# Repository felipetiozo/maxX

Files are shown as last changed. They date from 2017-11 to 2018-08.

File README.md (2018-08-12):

# maxX
Braço Robótico para fins educacionais
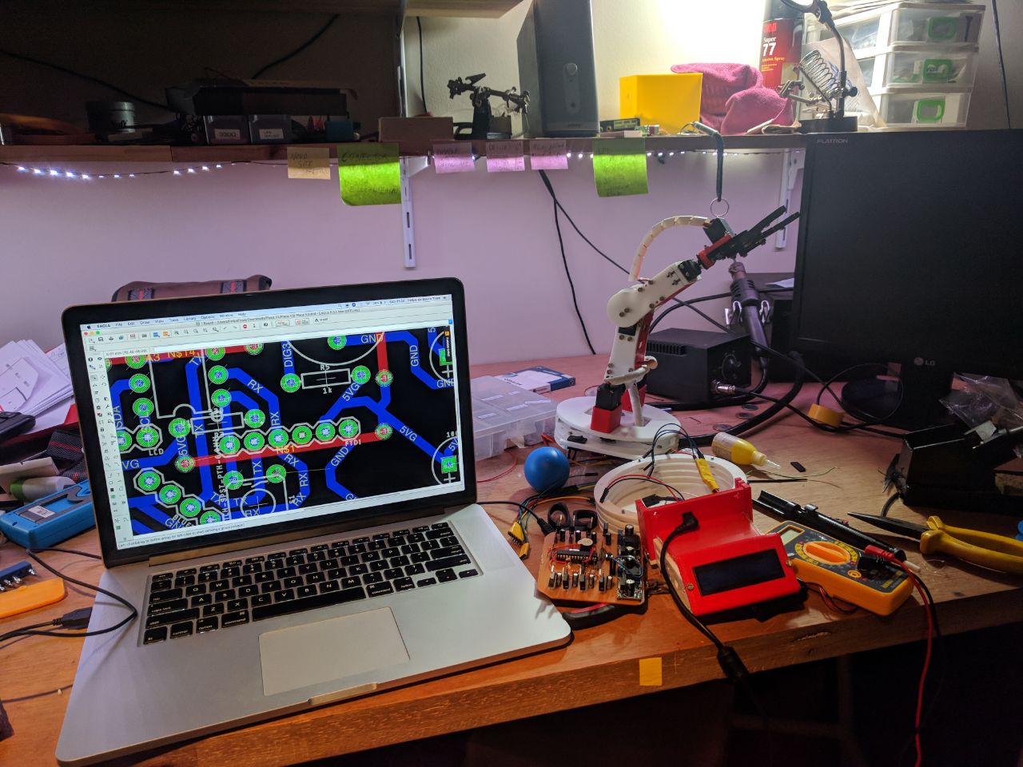
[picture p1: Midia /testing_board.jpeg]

<p align="center";> <b> Dia de testes do braço </b> </p>

# Divisões do projeto
* [`Software`](https://github.com/felipetiozo/maxX/tree/master/Software): Contem todas bibliotecas e código final do braço.
* [`Eletronica`](https://github.com/felipetiozo/maxX/tree/master/Eletronica): Possui todo esquema eletronico e o modelo final da PCB.
* [`Mecânica`](https://github.com/felipetiozo/maxX/tree/master/Mecanica): Todos arquivos .sldprt e .dxf do projeto.

## Eletronica
A PCB (Printed board circuit) do projeto foi construida no software [EAGLE(v8.3.1)](https://www.autodesk.com/products/eagle/overview) e fresada em uma mini cnc. [(Othermill)](https://www.bantamtools.com/)
### Lista de materiais 
| Qtd | Item | Loja | R$ |
|-----|---|-----|-----|
| 6 | MG995 Servo Motor | [Jsumo](http://www.jsumo.com/mg995-metal-gear-rc-servo-motor-towerpro) | 30,00 | 
| 1 | ATmega328P | [B.E](http://www.baudaeletronica.com.br/kit-arduino-atmega328p-bootloader.html) | 17,81 | 
| 2 | Encoder Decoder KY-040 | [Robocore](https://www.pololu.com/product/713) | 11,00 | 
| 1 | LCD 16x2 i2c | [Robocore](https://www.robocore.net/loja/produtos/lcd-16x2-5v-com-interface-i2c.html) | 49,00 | 
| 1 | FTDI Basic Breakout - 3.3V | [Sparkfun](https://www.sparkfun.com/products/9873) | 38,00 | 
| 2 | LM2596 | [B.E](http://www.baudaeletronica.com.br/modulo-regulador-de-tensao-lm2596.html) | 10,97 | 
| 1 | Fonte 12V 3A | [B.E](http://www.baudaeletronica.com.br/fonte-chaveada-12vdc-3a.html) | 48,37 | 

## Mecânica
O projeto mecânico foi desenvolvido no software de CAD [SolidWorks](http://www.solidworksbrasil.com.br/) e foi construido em 5 versões até chegar a final. Todas as peças foram impressas em 3D e cortadas em máquinas de corte a laser.

### Lista de materiais
| Qtd | Item | Loja | R$ |
|-----|---|-----|-----|
| 1 | Garra Robótica Croc | [Robocore](https://www.robocore.net/loja/produtos/garra-robotica-croc.html) | 29,00 | 
| 2 | Ball Caster with 3/8″ Metal Ball | [Pololu](https://www.pololu.com/product/951) | 6,50 | 

## Software
O software foi desenvolvido em cima da IDE [Arduino](https://www.arduino.cc/) e está dividido em diversas funções para uma utilização mais fácil.

# Contribuidores

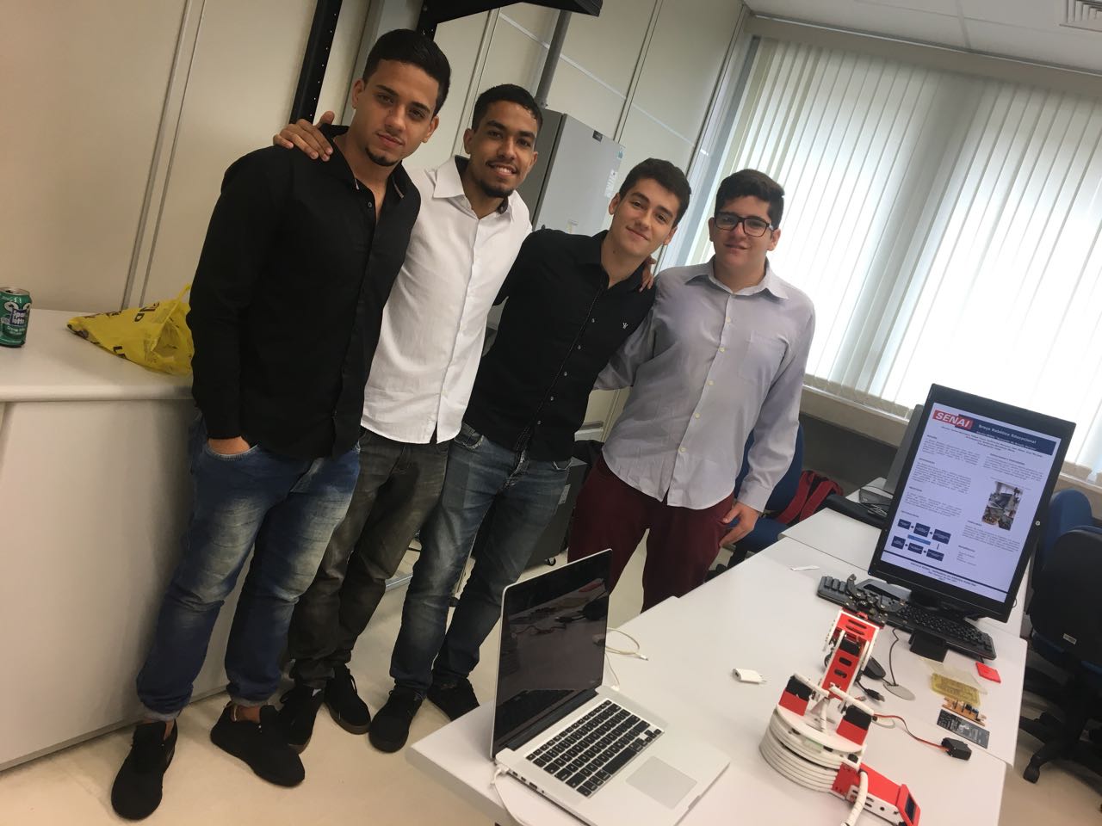
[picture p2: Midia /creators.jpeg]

<p align="center";> <b> Participantes do grupo </b> </p>

* [Felipe Tiozo](https://github.com/felipetiozo)
* [Igor Sousa](https://www.linkedin.com/in/igorsousa/)
* [Guilherme Basilio](https://www.facebook.com/guilherme.basilio.969)
* [Carlos Lima](https://www.facebook.com/profile.php?id=100004150566418)

## Agradecimentos
* [Engenhoteca](http://engenhoteca.com.br/)
* [João Pedro](https://github.com/joaopedrovbs)
* [Felipe Silva](https://github.com/feosilva)
* [Marcos Oliveira](https://github.com/marcosdeoliveira)
* [Tenda Digital](http://tenda.digital/)

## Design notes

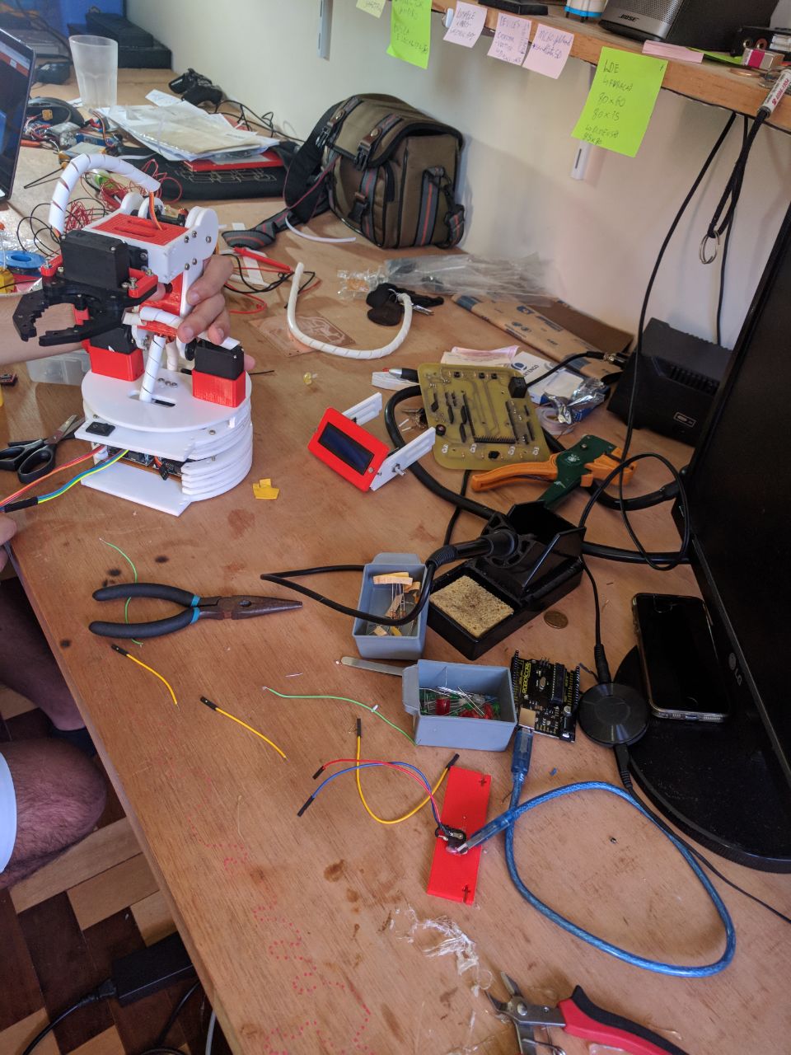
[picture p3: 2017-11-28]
Midia /working_on_mechanics2.jpeg

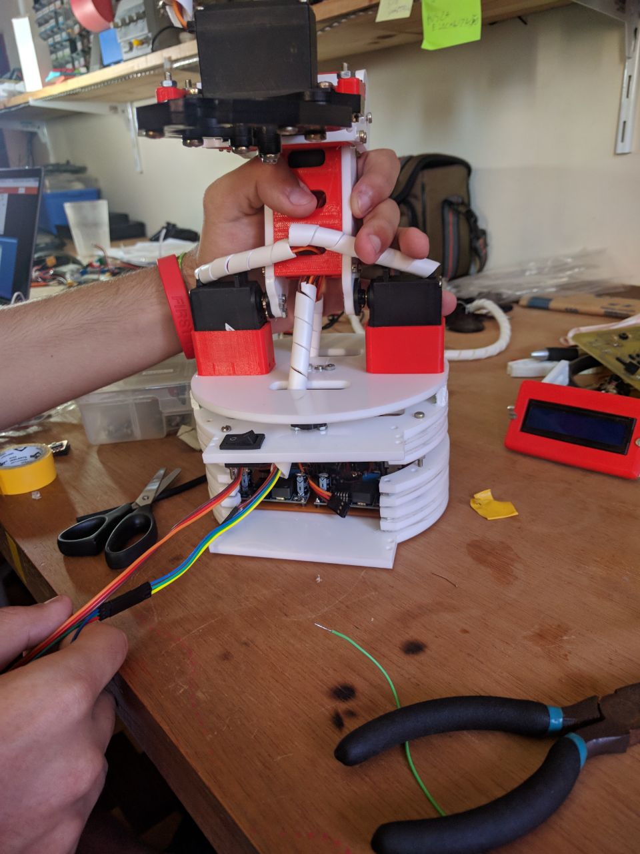
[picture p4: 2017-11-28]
Midia /working_on_mechanics.jpeg

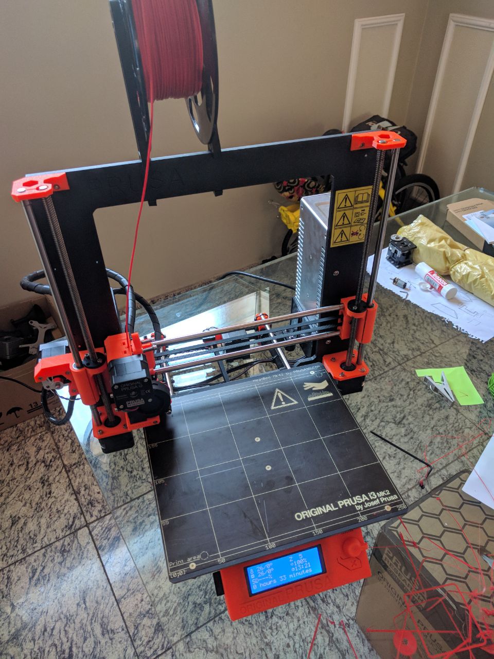
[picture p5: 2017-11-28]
Midia /prusai3mk2.jpeg

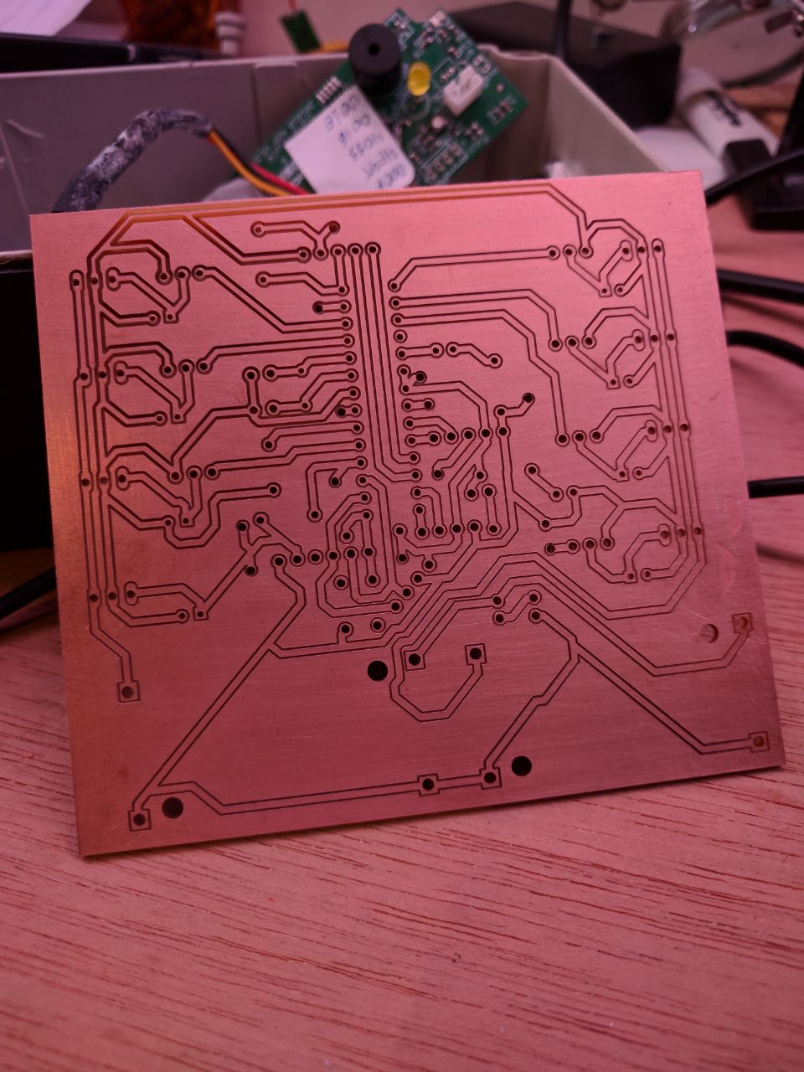
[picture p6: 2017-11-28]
Midia /board.jpeg

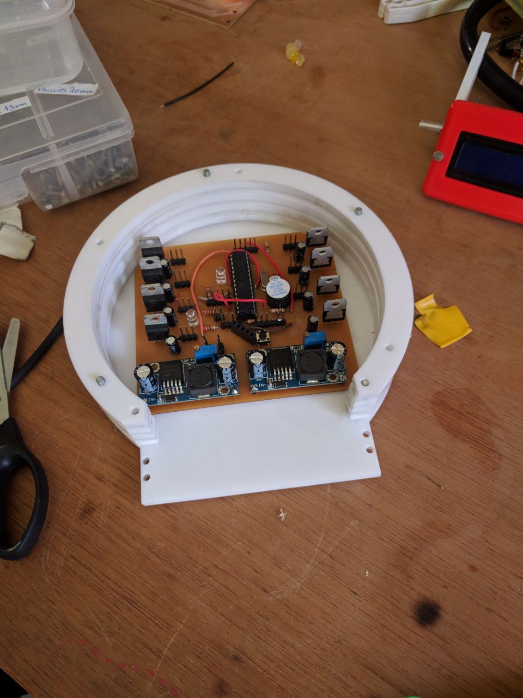
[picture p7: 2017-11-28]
Midia /final_board.jpeg

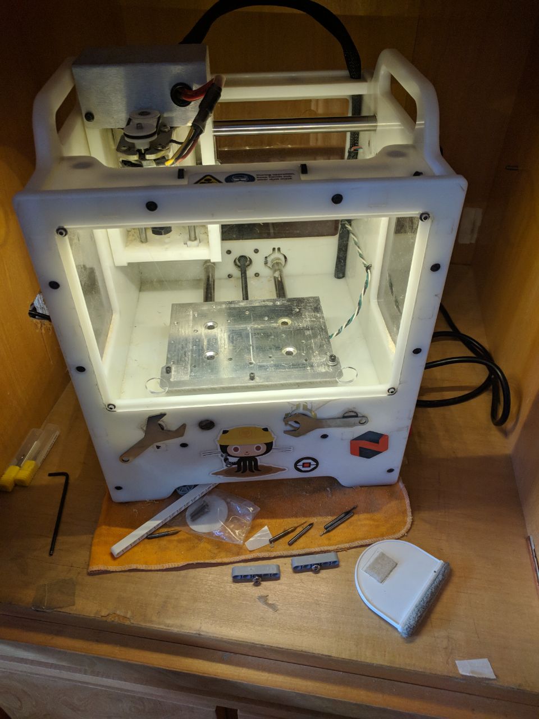
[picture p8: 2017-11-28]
Midia /othermill.jpeg

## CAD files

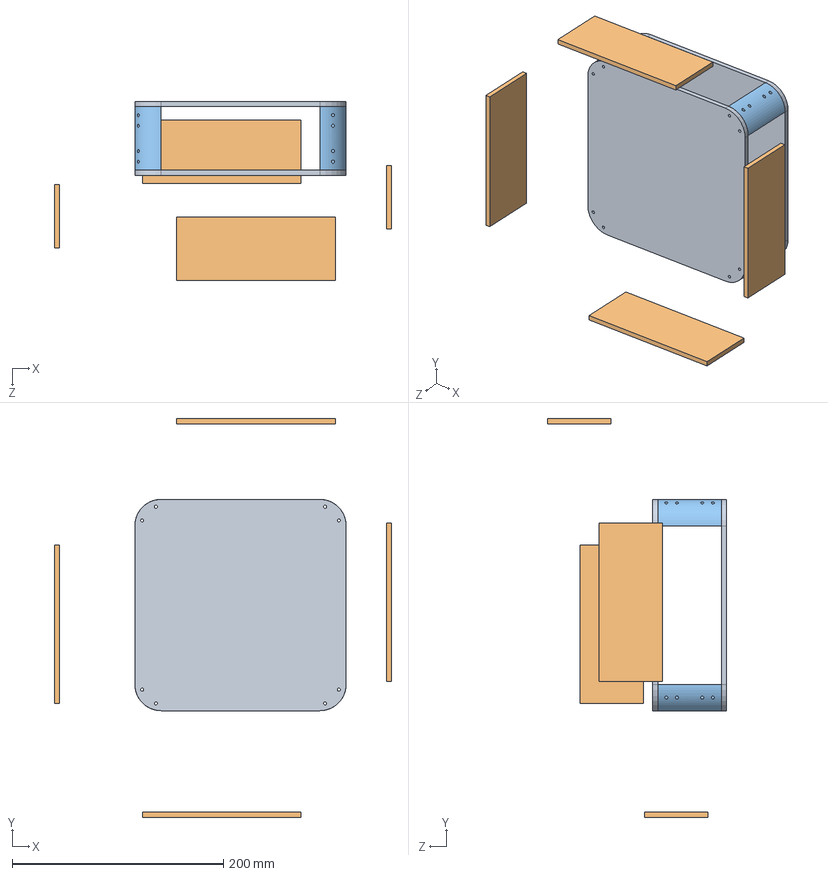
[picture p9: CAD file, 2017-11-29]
Mechanics/SolidWorks/Braço.SLDASM
319.0 x 377.4 x 169.4 mm
Cima Baixo base x 2
Parede base x 4
Angulo base x 4

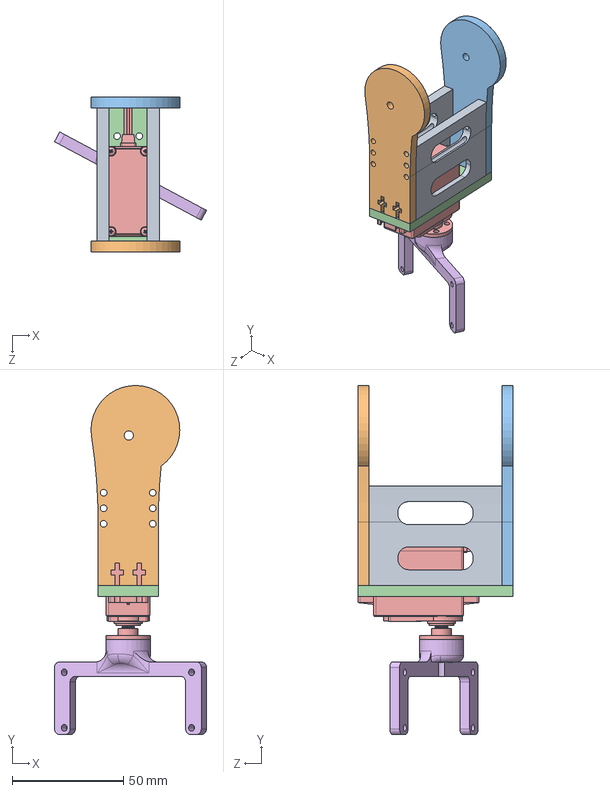
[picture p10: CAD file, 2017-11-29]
Mechanics/SolidWorks/JuntaSecundaria].SLDASM
68.5 x 157.2 x 70.0 mm
PSL esquerda x 2
PS DIREITA
PS ESQUERDA
SuporteServoGarra
Servo-MG-995
SuporteGarra

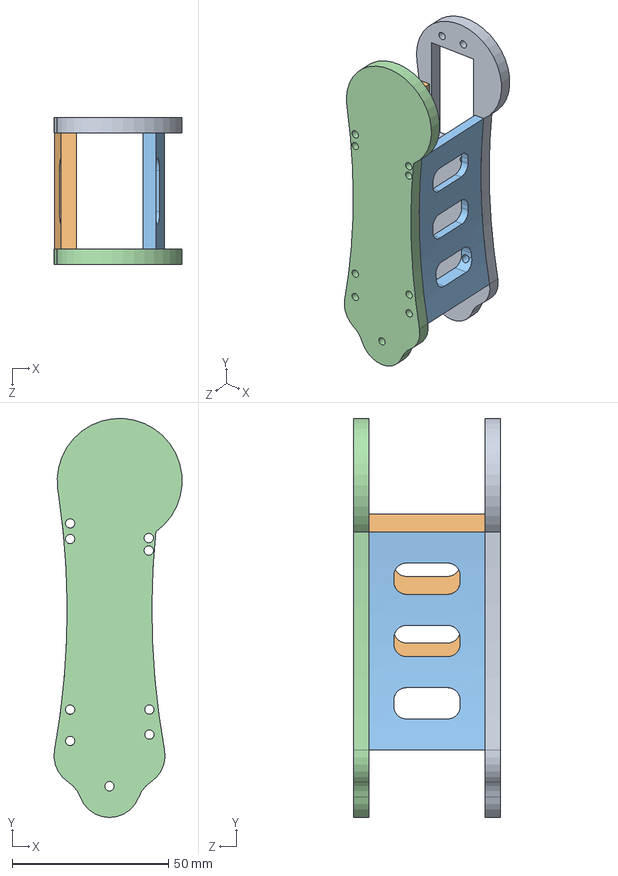
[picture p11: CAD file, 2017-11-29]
Mechanics/SolidWorks/JuntaPrincpal.SLDASM
41.0 x 127.7 x 47.2 mm
TT DIREITA
H1
H2
TT ESQUERDA

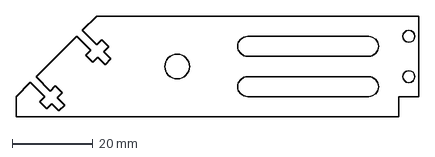
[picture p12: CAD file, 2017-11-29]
Mechanics/.DXF/LateralLCDx2.DXF
100.0 x 25.0 mm

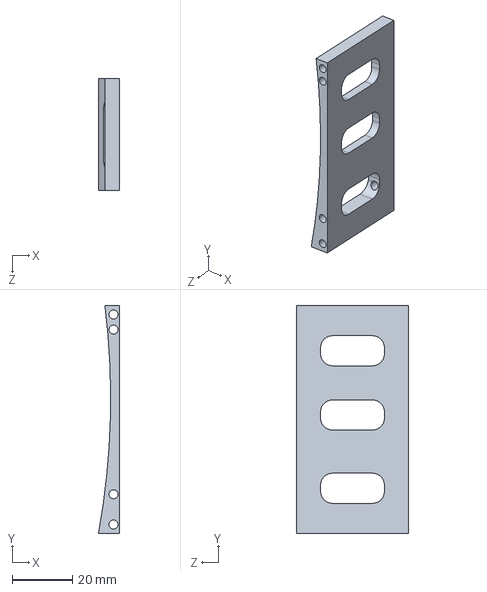
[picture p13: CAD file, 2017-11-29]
Mechanics/SolidWorks/H1.SLDPRT
7.02 x 75.6 x 37.2 mm

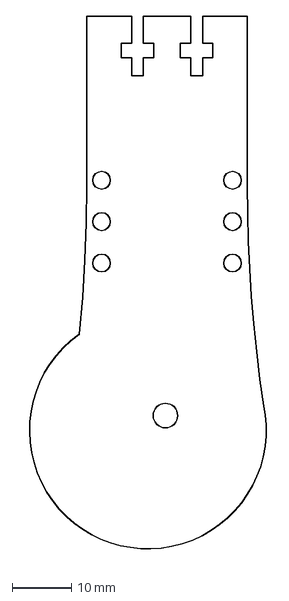
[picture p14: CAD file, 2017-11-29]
Mechanics/.DXF/PSDIRx1.DXF
43.4 x 92.0 mm

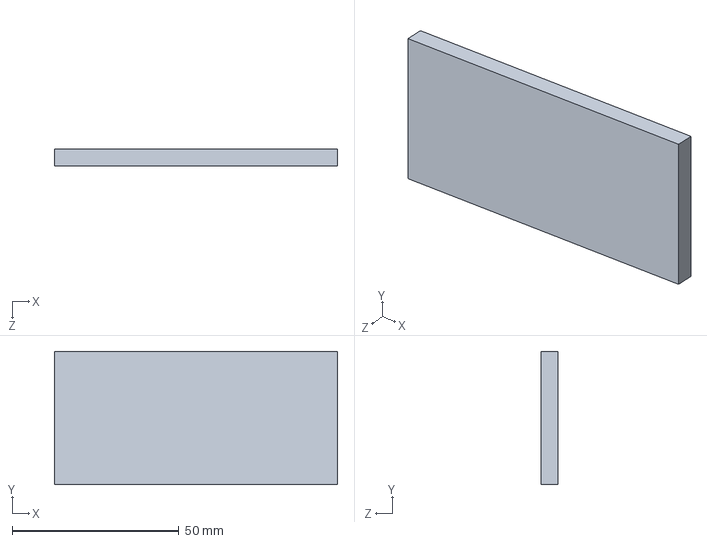
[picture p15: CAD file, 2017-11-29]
Mechanics/SolidWorks/Peça5.SLDPRT
84.9 x 40.0 x 5.00 mm

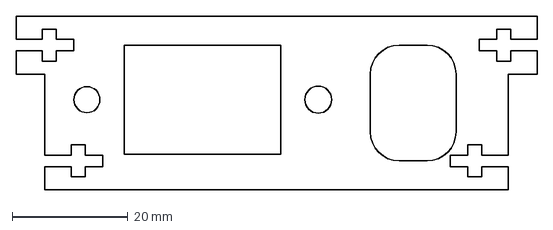
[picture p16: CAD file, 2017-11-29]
Mechanics/.DXF/FrenteBasex1.DXF
90.1 x 30.0 mm

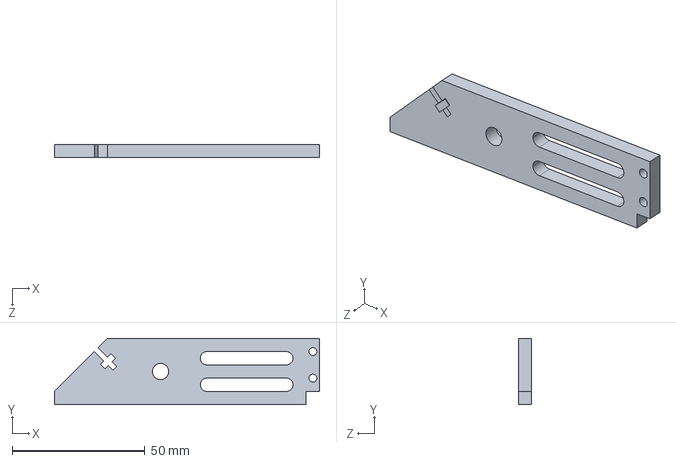
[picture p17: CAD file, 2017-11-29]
Mechanics/SolidWorks/Lateral lcd.SLDPRT
100.0 x 25.0 x 5.00 mm

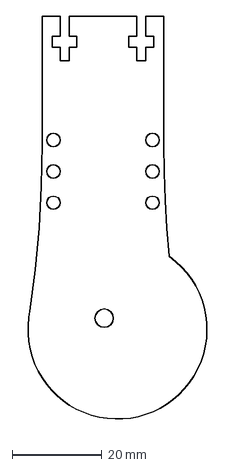
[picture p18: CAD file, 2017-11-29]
Mechanics/.DXF/PSESQx1.DXF
43.4 x 92.0 mm

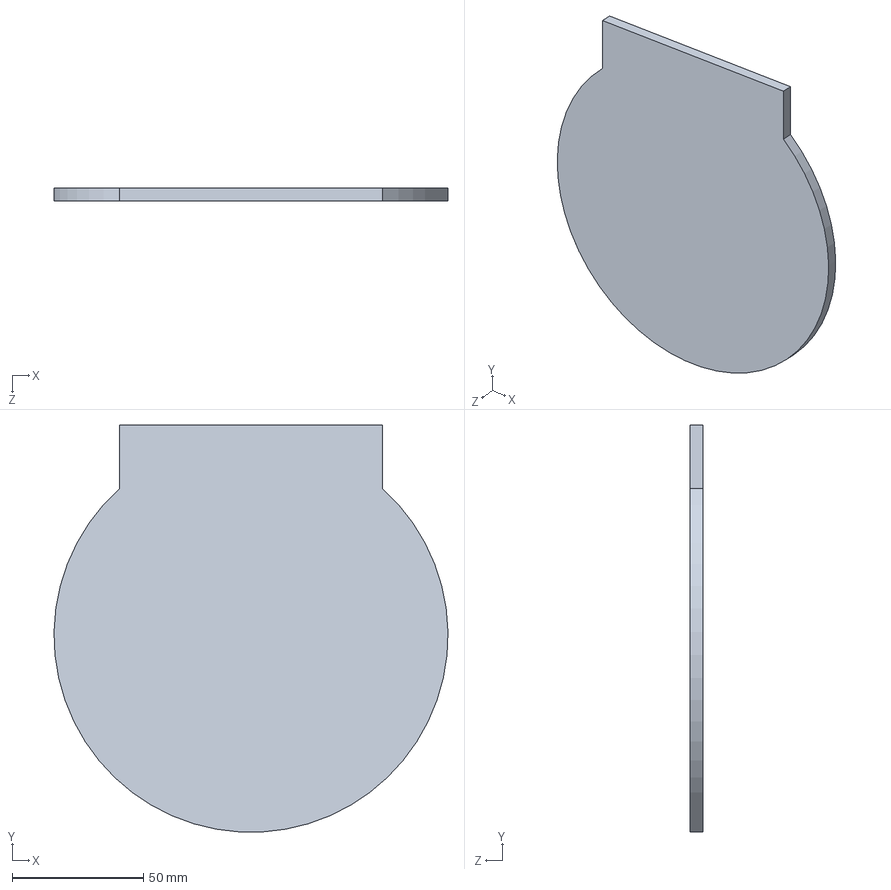
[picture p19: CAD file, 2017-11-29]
Mechanics/SolidWorks/Cima Baixo base.SLDPRT
150.0 x 154.9 x 5.00 mm

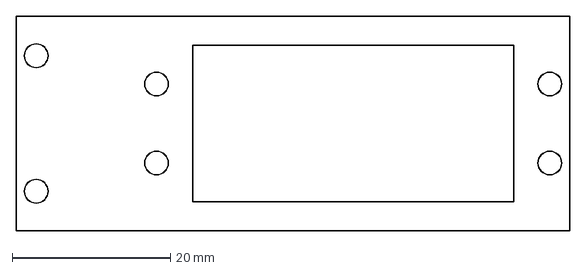
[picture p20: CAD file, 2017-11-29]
Mechanics/.DXF/SuporteServoGarrax1.DXF
70.0 x 27.1 mm

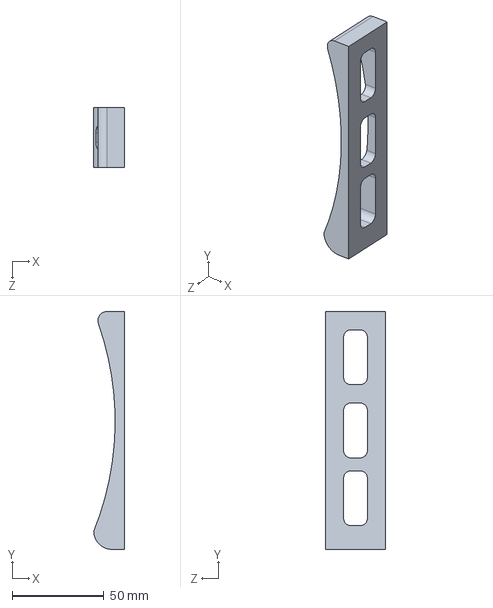
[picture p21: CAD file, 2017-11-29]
Mechanics/SolidWorks/H baixon.SLDPRT
16.7 x 130.0 x 33.0 mm

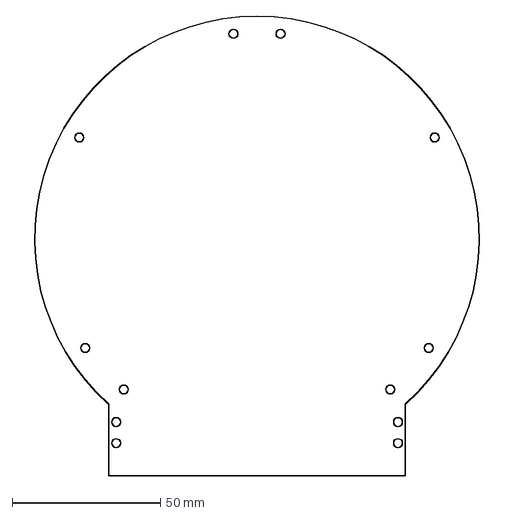
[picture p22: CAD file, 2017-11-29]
Mechanics/.DXF/BaixoBasex1.DXF
162.3 x 155.0 mm

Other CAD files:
Mechanics/SolidWorks/H baixo.SLDPRT
Mechanics/.DXF/TTESx1.DXF
Mechanics/SolidWorks/Ballcaster.SLDPRT
Mechanics/.DXF/BaseRedondax1.DXF
Mechanics/.DXF/CimaBasex1.DXF
Mechanics/.DXF/FrenteLCDx1.DXF
Mechanics/.DXF/LateralBasex2.DXF
Mechanics/.DXF/ParteAcrilicoBasex2.DXF
Mechanics/.DXF/TTDIRx1.DXF
Mechanics/SolidWorks/Alinhamento base baixo.SLDPRT
Mechanics/SolidWorks/Angulo base.SLDPRT
Mechanics/SolidWorks/Baixo base.SLDPRT
Mechanics/SolidWorks/Braço(1).SLDASM
Mechanics/SolidWorks/Cima base.SLDPRT
Mechanics/SolidWorks/FrenteBase.SLDPRT
Mechanics/SolidWorks/FrenteLCD.SLDPRT
Mechanics/SolidWorks/H2.SLDPRT
Mechanics/SolidWorks/LCDScreen.SLDPRT
Mechanics/SolidWorks/Lateral Base.SLDPRT
Mechanics/SolidWorks/PCB.SLDPRT
Mechanics/SolidWorks/PS DIREITA.SLDPRT
Mechanics/SolidWorks/PS ESQUERDA.SLDPRT
Mechanics/SolidWorks/PSL esquerda.SLDPRT
Mechanics/SolidWorks/Parede base.SLDPRT
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

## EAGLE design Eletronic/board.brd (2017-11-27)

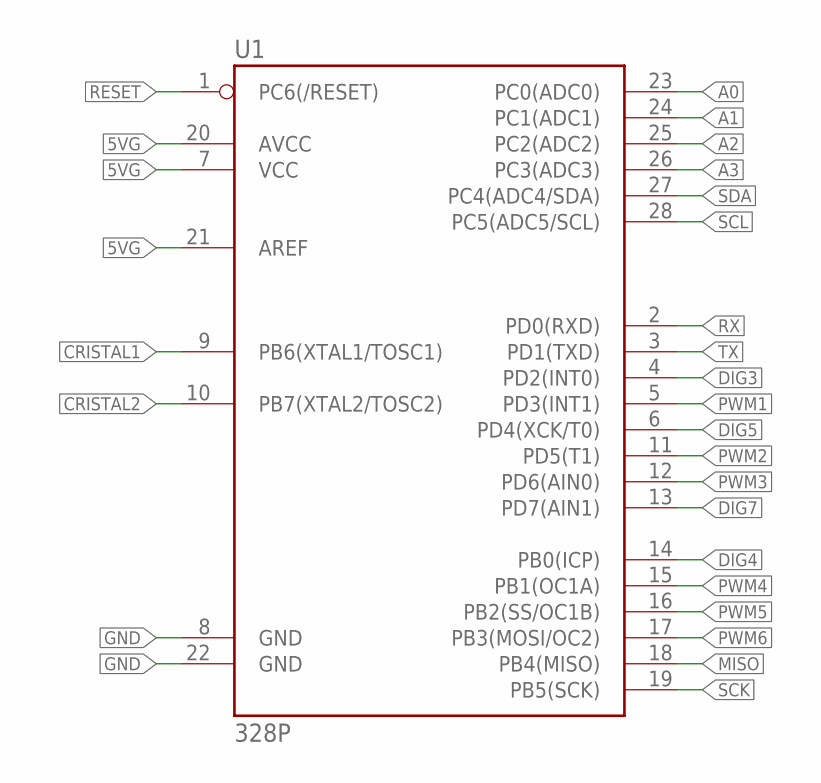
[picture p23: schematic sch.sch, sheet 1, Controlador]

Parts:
U1: 328P; DIP28

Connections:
5VG: U1.7 (VCC), U1.20 (AVCC), U1.21 (AREF); also elsewhere on the board
A0: U1.23 (PC0(ADC0)); also elsewhere on the board
A1: U1.24 (PC1(ADC1)); also elsewhere on the board
A2: U1.25 (PC2(ADC2)); also elsewhere on the board
A3: U1.26 (PC3(ADC3)); also elsewhere on the board
CRISTAL1: U1.9 (PB6(XTAL1/TOSC1)); also elsewhere on the board
CRISTAL2: U1.10 (PB7(XTAL2/TOSC2)); also elsewhere on the board
DIG3: U1.4 (PD2(INT0)); also elsewhere on the board
DIG4: U1.14 (PB0(ICP)); also elsewhere on the board
DIG5: U1.6 (PD4(XCK/T0)); also elsewhere on the board
DIG7: U1.13 (PD7(AIN1)); also elsewhere on the board
GND: U1.8 (GND), U1.22 (GND); also elsewhere on the board
MISO: U1.18 (PB4(MISO))
PWM1: U1.5 (PD3(INT1)); also elsewhere on the board
PWM2: U1.11 (PD5(T1)); also elsewhere on the board
PWM3: U1.12 (PD6(AIN0)); also elsewhere on the board
PWM4: U1.15 (PB1(OC1A)); also elsewhere on the board
PWM5: U1.16 (PB2(SS/OC1B)); also elsewhere on the board
PWM6: U1.17 (PB3(MOSI/OC2)); also elsewhere on the board
RESET: U1.1 (PC6(/RESET)); also elsewhere on the board
RX: U1.2 (PD0(RXD)); also elsewhere on the board
SCK: U1.19 (PB5(SCK)); also elsewhere on the board
SCL: U1.28 (PC5(ADC5/SCL)); also elsewhere on the board
SDA: U1.27 (PC4(ADC4/SDA)); also elsewhere on the board
TX: U1.3 (PD1(TXD)); also elsewhere on the board

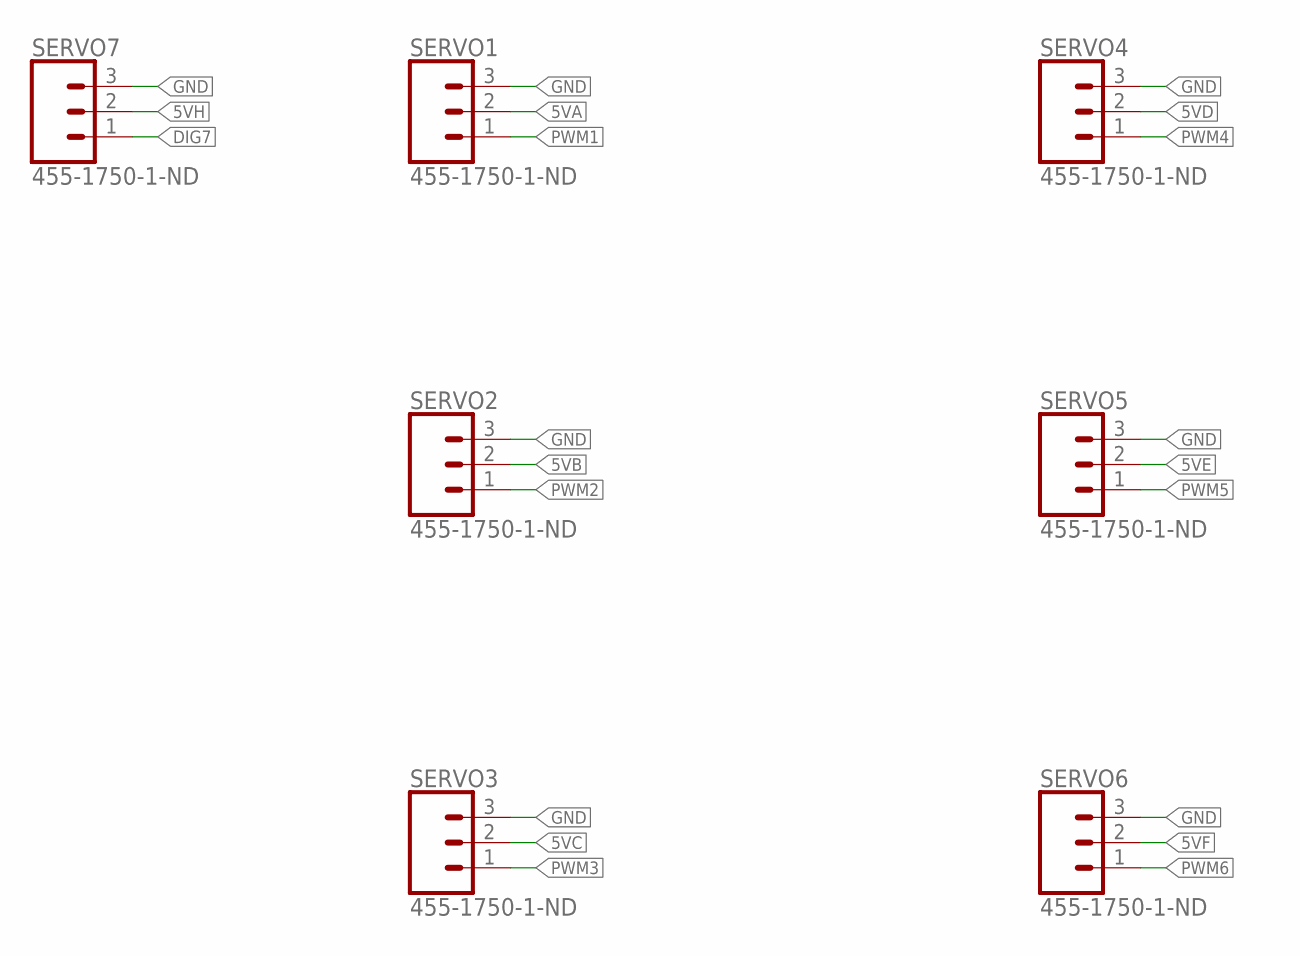
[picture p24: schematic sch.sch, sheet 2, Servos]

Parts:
SERVO1, SERVO2, SERVO3, SERVO4, SERVO5, SERVO6, SERVO7: 455-1750-1-ND; 1X03

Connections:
5VA: SERVO1.2; also elsewhere on the board
5VB: SERVO2.2; also elsewhere on the board
5VC: SERVO3.2; also elsewhere on the board
5VD: SERVO4.2; also elsewhere on the board
5VE: SERVO5.2; also elsewhere on the board
5VF: SERVO6.2; also elsewhere on the board
5VH: SERVO7.2; also elsewhere on the board
DIG7: SERVO7.1; also elsewhere on the board
GND: SERVO1.3, SERVO2.3, SERVO3.3, SERVO4.3, SERVO5.3, SERVO6.3, SERVO7.3; also elsewhere on the board
PWM1: SERVO1.1; also elsewhere on the board
PWM2: SERVO2.1; also elsewhere on the board
PWM3: SERVO3.1; also elsewhere on the board
PWM4: SERVO4.1; also elsewhere on the board
PWM5: SERVO5.1; also elsewhere on the board
PWM6: SERVO6.1; also elsewhere on the board

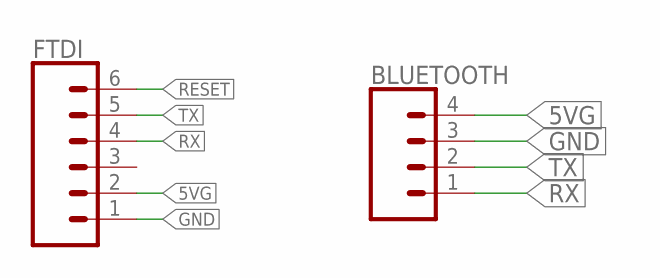
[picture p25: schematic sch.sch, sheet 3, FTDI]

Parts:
BLUETOOTH: CONN_04; 1X04
FTDI: CONN_06SILK_FEMALE_PTH; 1X06

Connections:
5VG: BLUETOOTH.4, FTDI.2; also elsewhere on the board
GND: BLUETOOTH.3, FTDI.1; also elsewhere on the board
RESET: FTDI.6; also elsewhere on the board
RX: BLUETOOTH.1, FTDI.4; also elsewhere on the board
TX: BLUETOOTH.2, FTDI.5; also elsewhere on the board

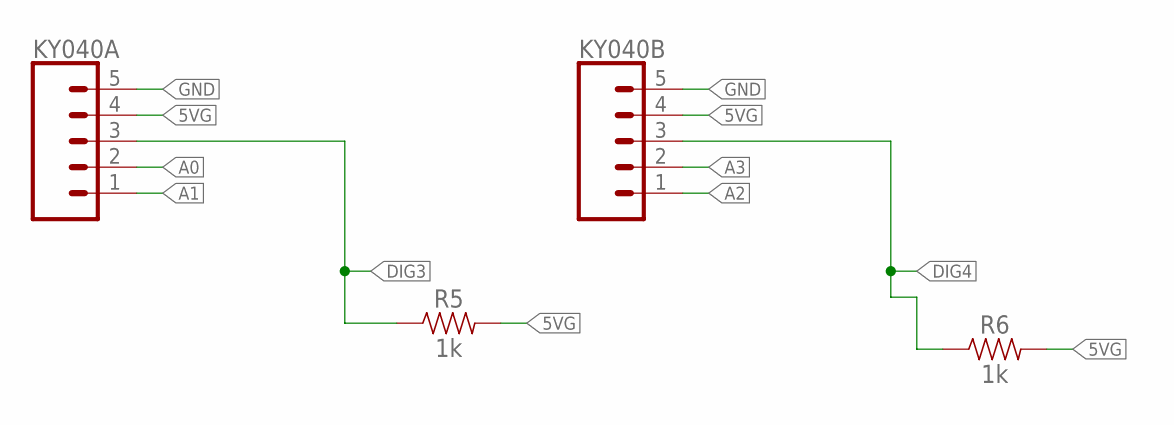
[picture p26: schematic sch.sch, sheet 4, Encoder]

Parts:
KY040A, KY040B: CONN_05; 1X05
R5, R6: 1k; AXIAL-0.3

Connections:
5VG: KY040A.4, KY040B.4, R5.P$2 (2), R6.P$2 (2); also elsewhere on the board
A0: KY040A.2; also elsewhere on the board
A1: KY040A.1; also elsewhere on the board
A2: KY040B.1; also elsewhere on the board
A3: KY040B.2; also elsewhere on the board
DIG3: KY040A.3, R5.P$1 (1); also elsewhere on the board
DIG4: KY040B.3, R6.P$1 (1); also elsewhere on the board
GND: KY040A.5, KY040B.5; also elsewhere on the board

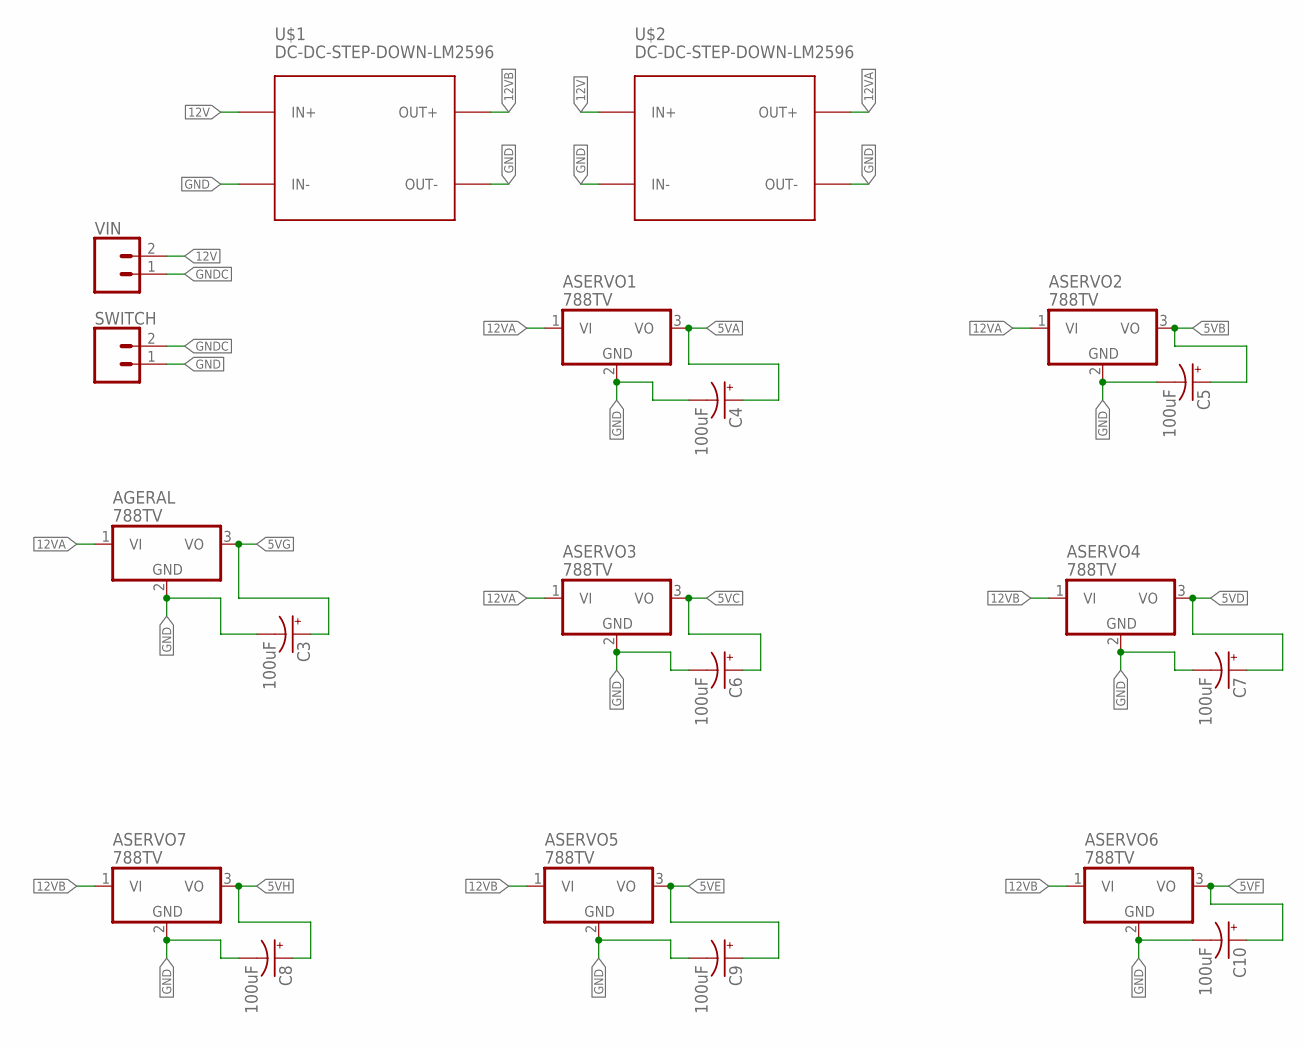
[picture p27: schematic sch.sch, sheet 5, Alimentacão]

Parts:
AGERAL: 788TV; TO220V
ASERVO1, ASERVO2, ASERVO3, ASERVO4, ASERVO5, ASERVO6, ASERVO7: 788TV; TO220V
C3, C4, C5, C6, C7, C8, C9, C10: 100uF; CPOL-RADIAL-2.5MM-6.5MM
SWITCH: CONN_02; 1X02
U$1, U$2: DC-DC-STEP-DOWN-LM2596
VIN: CONN_02; 1X02

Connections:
5VA: ASERVO1.3 (VO), C4.1 (+); also elsewhere on the board
5VB: ASERVO2.3 (VO), C5.1 (+); also elsewhere on the board
5VC: ASERVO3.3 (VO), C6.1 (+); also elsewhere on the board
5VD: ASERVO4.3 (VO), C7.1 (+); also elsewhere on the board
5VE: ASERVO5.3 (VO), C9.1 (+); also elsewhere on the board
5VF: ASERVO6.3 (VO), C10.1 (+); also elsewhere on the board
5VG: AGERAL.3 (VO), C3.1 (+); also elsewhere on the board
5VH: ASERVO7.3 (VO), C8.1 (+); also elsewhere on the board
12V: U$1.IN+, U$2.IN+, VIN.2
12VA: AGERAL.1 (VI), ASERVO1.1 (VI), ASERVO2.1 (VI), ASERVO3.1 (VI), U$2.OUT+
12VB: ASERVO4.1 (VI), ASERVO5.1 (VI), ASERVO6.1 (VI), ASERVO7.1 (VI), U$1.OUT+
GND: AGERAL.2 (GND), ASERVO1.2 (GND), ASERVO2.2 (GND), ASERVO3.2 (GND), ASERVO4.2 (GND), ASERVO5.2 (GND), ASERVO6.2 (GND), ASERVO7.2 (GND), C3.2 (-), C4.2 (-), C5.2 (-), C6.2 (-), C7.2 (-), C8.2 (-), C9.2 (-), C10.2 (-), SWITCH.1, U$1.IN-, U$1.OUT-, U$2.IN-, U$2.OUT-; also elsewhere on the board
GNDC: SWITCH.2, VIN.1

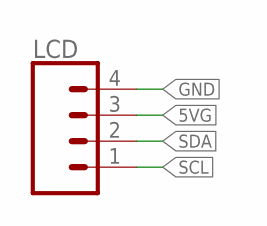
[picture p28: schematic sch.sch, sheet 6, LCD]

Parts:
LCD: CONN_04; 1X04

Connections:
5VG: LCD.3; also elsewhere on the board
GND: LCD.4; also elsewhere on the board
SCL: LCD.1; also elsewhere on the board
SDA: LCD.2; also elsewhere on the board

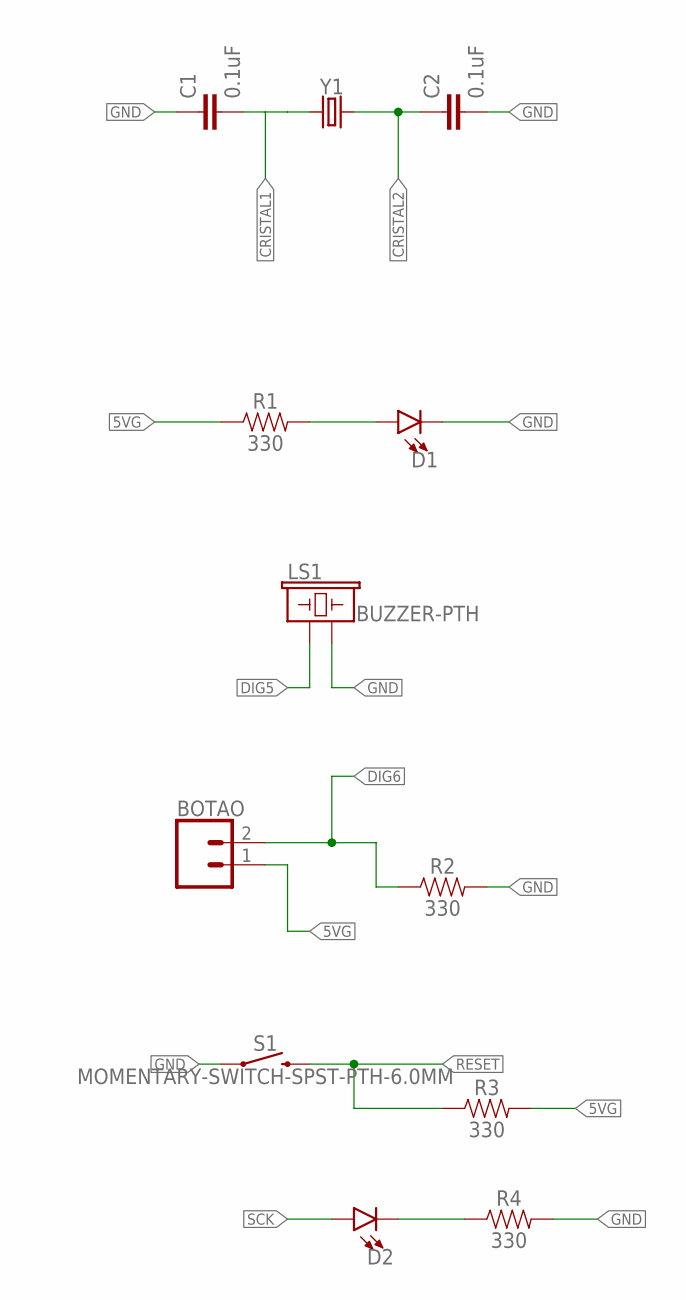
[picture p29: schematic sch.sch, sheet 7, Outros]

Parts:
BOTAO: CONN_02; 1X02
C1, C2: 0.1uF; CAP-PTH-SMALL-KIT
D1, D2: LED5MM; LED_5MM
LS1: BUZZER-PTH; BUZZER-12MM
R1, R2, R3, R4: 330; AXIAL-0.3
S1: MOMENTARY-SWITCH-SPST-PTH-6.0MM; TACTILE_SWITCH_PTH_6.0MM
Y1: CRYSTALPTH-HC49US; HC49US

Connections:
5VG: BOTAO.1, R1.P$1 (1), R3.P$2 (2); also elsewhere on the board
CRISTAL1: C1.2, Y1.1; also elsewhere on the board
CRISTAL2: C2.1, Y1.2; also elsewhere on the board
DIG5: LS1.+ (1); also elsewhere on the board
DIG6: BOTAO.2, R2.P$1 (1)
GND: C1.1, C2.2, D1.K (C), LS1.- (2), R2.P$2 (2), R4.P$2 (2), S1.1; also elsewhere on the board
unnamed: D1.A, R1.P$2 (2)
unnamed: D2.K (C), R4.P$1 (1)
RESET: R3.P$1 (1), S1.3 (2); also elsewhere on the board
SCK: D2.A; also elsewhere on the board

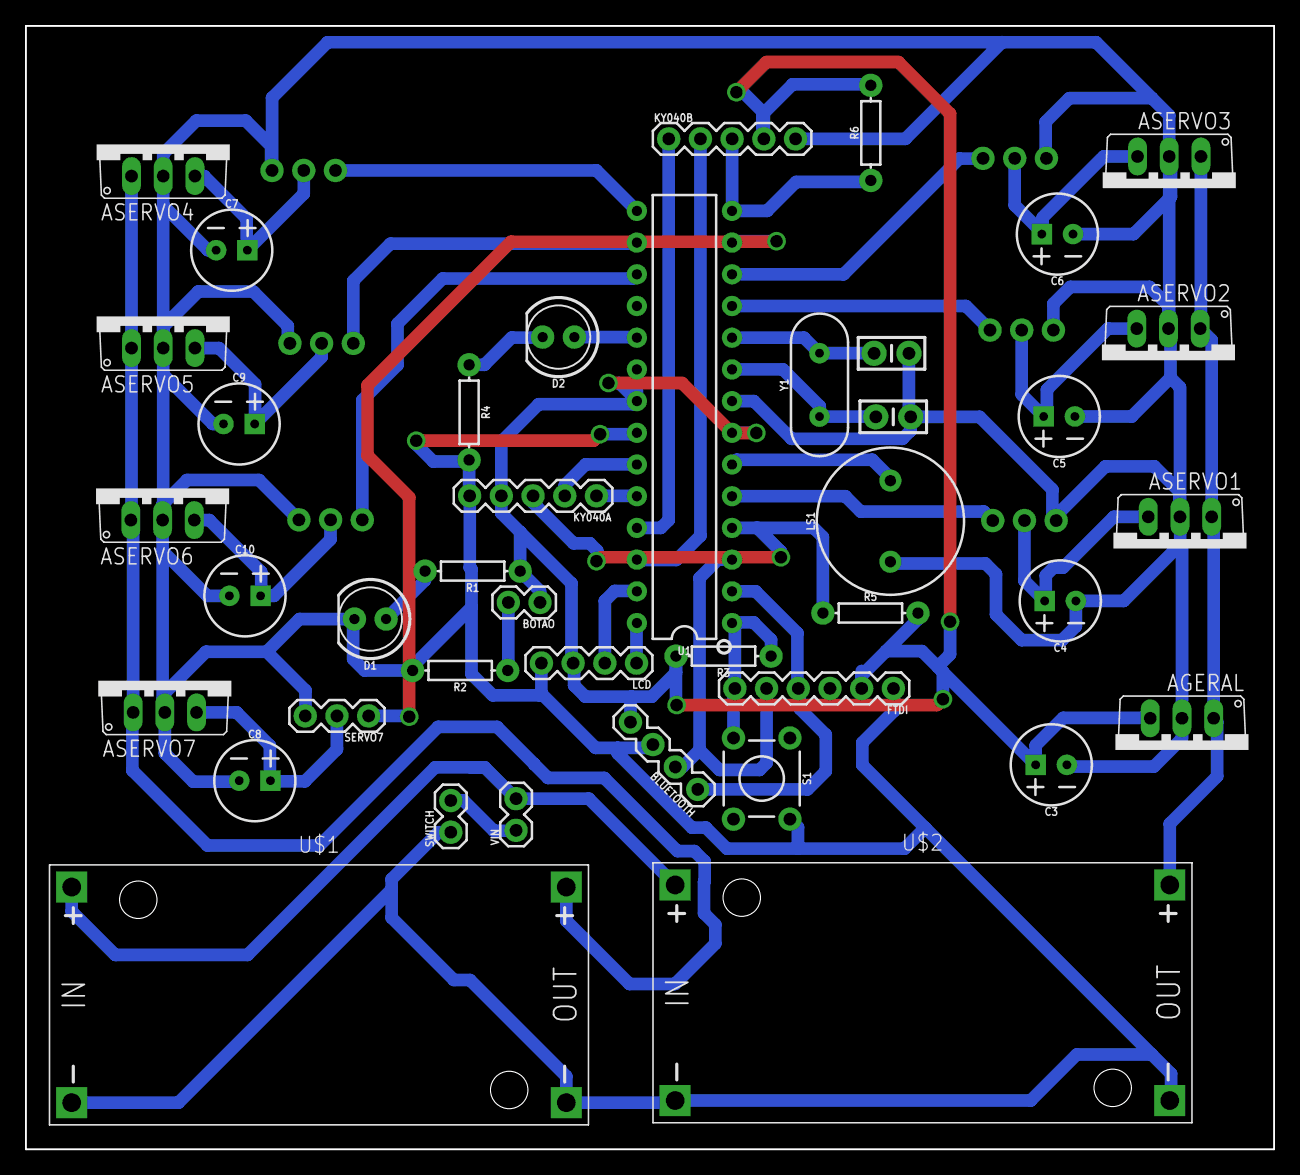
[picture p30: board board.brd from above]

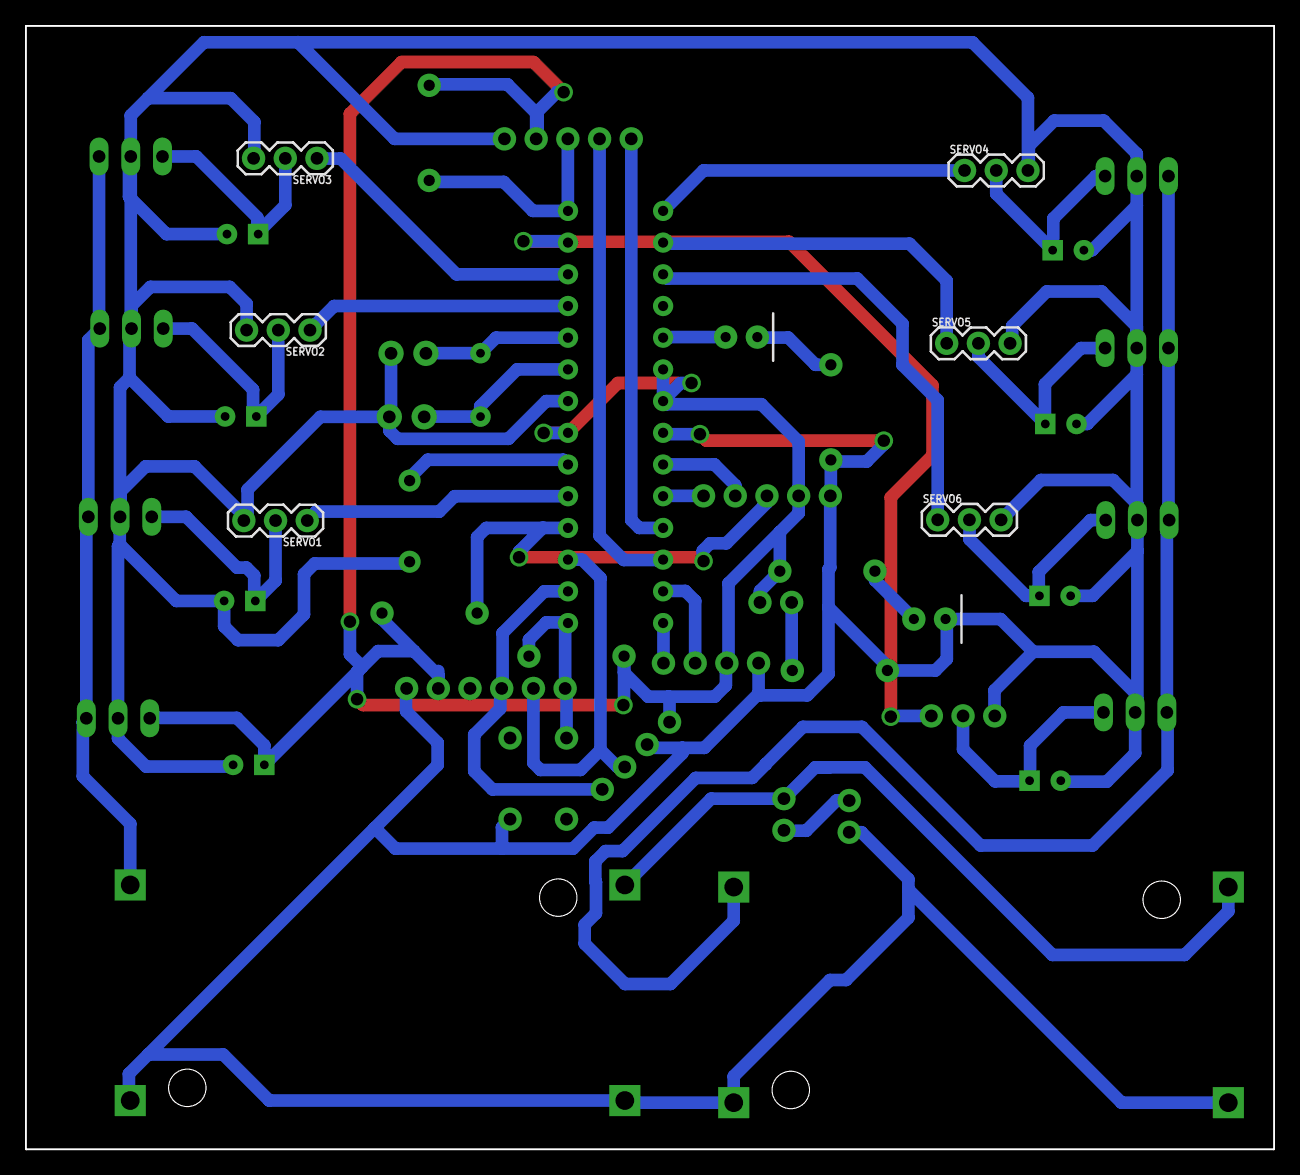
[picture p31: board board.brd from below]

Board: 2 copper layers, 100.0 x 90.0 mm, 47 parts (6 on the bottom side), 38 nets.

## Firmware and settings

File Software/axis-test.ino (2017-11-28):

/*
  Servo giro garra porta 5

  Servo 6 ????

  Servo 9    garra   110 - 180

  Servo 10 Junta principal

  Servo 11 Junta Secundaria

  Servo 7 Base

  teste

*/
#include <Wire.h>
#include <LiquidCrystal_I2C.h>
#include <Servo.h>
#include <RotaryEncoder.h>

LiquidCrystal_I2C lcd(0x27, 20, 4);

RotaryEncoder encoder(A2, A3);

Servo GiroGarra;
Servo Garra;
Servo Base;
Servo JuntaPrincipal;
Servo Secundaria;


void apitar() {

  digitalWrite(4, HIGH);
  delay(50);
  digitalWrite(4, LOW);
  delay(50);
  digitalWrite(4, HIGH);
  delay(50);
  digitalWrite(4, LOW);
  delay(50);
  digitalWrite(4, HIGH);
  delay(50);
  digitalWrite(4, LOW);
  delay(50);
}

void inicio() {
  pinMode(4, OUTPUT);
  lcd.init();
  lcd.init();
  lcd.backlight();
  lcd.setCursor(2, 0);
  lcd.print("Inicializando");
  delay(10);
  lcd.setCursor(0, 1);
  lcd.print("#");
  int t = 10;
  delay(t);
  apitar();
  lcd.setCursor(0, 1);
  lcd.print("##");
  delay(t);
  apitar();
  lcd.setCursor(0, 1);
  lcd.print("###");
  delay(t);
  apitar();
  lcd.setCursor(0, 1);
  lcd.print("####");
  delay(t);
  apitar();
  lcd.setCursor(0, 1);
  lcd.print("#####");
  delay(t);
  apitar();
  lcd.setCursor(0, 1);
  lcd.print("######");
  delay(t);
  apitar();
  lcd.setCursor(0, 1);
  lcd.print("#######");
  delay(t);
  apitar();
  lcd.setCursor(0, 1);
  lcd.print("########");
  delay(t);
  apitar();
  lcd.setCursor(0, 1);
  lcd.print("#########");
  delay(t);
  apitar();
  lcd.setCursor(0, 1);
  lcd.print("##########");
  delay(t);
  apitar();
  lcd.setCursor(0, 1);
  lcd.print("###########");
  delay(t);
  apitar();
  lcd.setCursor(0, 1);
  lcd.print("############");
  delay(t);
  apitar();
  lcd.setCursor(0, 1);
  lcd.print("#############");
  delay(t);
  apitar();
  lcd.setCursor(0, 1);
  lcd.print("##############");
  delay(t);
  apitar();
  lcd.setCursor(0, 1);
  lcd.print("###############");
  delay(t);
  apitar();
  lcd.setCursor(0, 1);
  lcd.print("################");
  delay(t);
  apitar();


}

void settings() {



}

void menu() {
  lcd.clear();
  lcd.setCursor(3, 0);
  lcd.print("MaxX Robot");
  lcd.setCursor(6, 1);
  lcd.print("V2.2");
  delay(3000);
  lcd.clear();
  lcd.setCursor(6, 0);
  lcd.print("Modo");
  lcd.setCursor(2, 1);
  lcd.print("Demonstracao");

}


void abrirgarra() {
  Garra.write(160);
  delay(2000);
}

void fechargarra() {
  Garra.write(100);
  delay(2000);
}

void demo1() {
  JuntaPrincipal.write(78);
  delay(2000);
  Base.write(110);
  delay(2000);
  Base.write(180);
  delay(2000);
  JuntaPrincipal.write(140);
  delay(2500);
  Garra.write(160);
  delay(2000);
  GiroGarra.write(60);
  delay(2000);
  Secundaria.write(31);
  delay(2500);
  Garra.write(100);
  delay(2000);

  // FECHOU GARRA COM ARGOLA


  Secundaria.write(90);
  delay(2500);
  JuntaPrincipal.write(90);
  delay(2000);
  Base.write(5);
  delay(2000);

  // VIROU BASE COM ARGOLA
  /* JuntaPrincipal.write(135);
    delay(2000);
    Secundaria.write(17);
    delay(2000);
    abrirgarra();
  */
  JuntaPrincipal.write(140);
  delay(2500);
  // Garra.write(160);
  //delay(2000);
  //GiroGarra.write(60);
  //delay(2000);
  Secundaria.write(31);
  delay(2500);
  abrirgarra();

  // LARGOU ARGOLA

  JuntaPrincipal.write(80);
  delay(2000);
  Base.write(110);
  delay(2000);
  apitar();
  apitar();
  apitar();

  // VOLTA PARA POSICAO
  Base.write(5);
  delay(2000);
  JuntaPrincipal.write(140);
  delay(2000);
  Secundaria.write(31);
  delay(2000);
  fechargarra();

  // PEGOU ARGOLA
  JuntaPrincipal.write(78);
  delay(2000);
  Base.write(180);
  delay(2000);
  JuntaPrincipal.write(140);
  delay(2500);
  Secundaria.write(31);
  delay(2500);
  abrirgarra();

  // LARGOU ARGOLA
  Secundaria.write(90);
  delay(2000);
  JuntaPrincipal.write(90);
  delay(2000);
  Base.write(110);
  delay(2000);




}
void posicaoinicial() {
  JuntaPrincipal.write(78);
  delay(1000);
  Base.write(110);
  delay(1000);
  apitar();
}

void posicaodireita() {
  Base.write(180);
  delay(1000);
}

void posicaoesquerda() {
  Base.write(5);
  delay(1000);
}

void abaixar() {
  JuntaPrincipal.write(140);
  delay(1000);
  Garra.write(160);
  delay(1000);
  GiroGarra.write(60);
  delay(1000);
  Secundaria.write(31);
  delay(1000);
  Garra.write(100);
  delay(1000);
  Secundaria.write(90);
  delay(1000);
  JuntaPrincipal.write(90);
  delay(1000);
}

void abaixar2() {
  JuntaPrincipal.write(180);
  delay(1000);
  Garra.write(180);
  delay(1000);
  Secundaria.write(79);
  delay(1000);
  Garra.write(110);
  delay(1000);
  Secundaria.write(90);
  delay(1000);
  JuntaPrincipal.write(90);
  delay(1000);
}

void abaixar3() {
  JuntaPrincipal.write(180);
  delay(1000);
  Garra.write(110);
  delay(1000);
  Secundaria.write(75);
  delay(1000);
  Garra.write(180);
  delay(1000);
  Secundaria.write(140);
  delay(1000);
 // JuntaPrincipal.write(140);
  //delay(1000);
  JuntaPrincipal.write(90);
  delay(1000);
}
void demo2() {
  posicaoinicial();
  posicaodireita();
  abaixar();
  posicaoinicial();
  posicaoesquerda();
  abaixar();
  posicaoinicial();
}

void demo3() {

  posicaoinicial();
  posicaodireita();
  abaixar2();
  posicaoinicial();
  posicaoesquerda();
  abaixar3();
  posicaoinicial();

  
  posicaoesquerda();
  abaixar2();
  posicaoinicial();
  posicaoesquerda();
  abaixar3();
  

}


void setup() {
  inicio();


  settings();

  GiroGarra.attach(6);
  delay(1000);
  Garra.attach(9);
  delay(1000);
  Base.attach(7);
  delay(1000);
  Secundaria.attach(11);
  delay(1000);
  JuntaPrincipal.attach(10);
  delay(1000);

  menu();






}


void loop() {

  //demo1();
  //demo2();
   demo3();



}

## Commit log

2017-11-27 Add maxx PCB
    [Placa V.5.brd, Placa V.5.sch]
2017-11-29 Added mechanical files
    [Alinhamento base baixo.SLDPRT, Angulo base.SLDPRT, Baixo base.SLDPRT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]
2017-11-29 Added some changes
    [Custos.xlsx]
2018-08-12 fix some titles
    [Alinhamento base baixo.SLDPRT, Angulo base.SLDPRT, Baixo base.SLDPRT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]

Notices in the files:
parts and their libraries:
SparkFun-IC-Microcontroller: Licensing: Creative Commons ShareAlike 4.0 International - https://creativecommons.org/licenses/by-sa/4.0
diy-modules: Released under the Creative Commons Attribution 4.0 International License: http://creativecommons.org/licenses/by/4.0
